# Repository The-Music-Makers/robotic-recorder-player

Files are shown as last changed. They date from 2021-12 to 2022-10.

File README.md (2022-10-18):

# Music Makers

## Robotic Recorder Player

This project is an open source hardware project that is intended to be an automated way to play a recorder instrument. Build it for yourself and use the [Python Interface](Python_Interface) to send your MIDI files to the robotic recorder player and hear them played on the recorder!

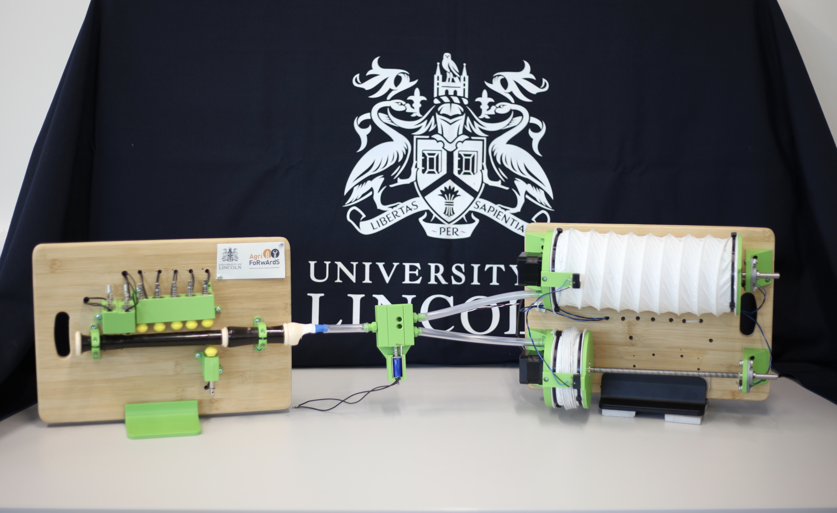
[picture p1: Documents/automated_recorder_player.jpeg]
robotic-recorder-player-image


### Demonstration

https://user-images.githubusercontent.com/53816688/196008536-8c850554-d10a-48c4-a584-36b9e6b4f8ee.mp4

### ICMC 2022 Presentation

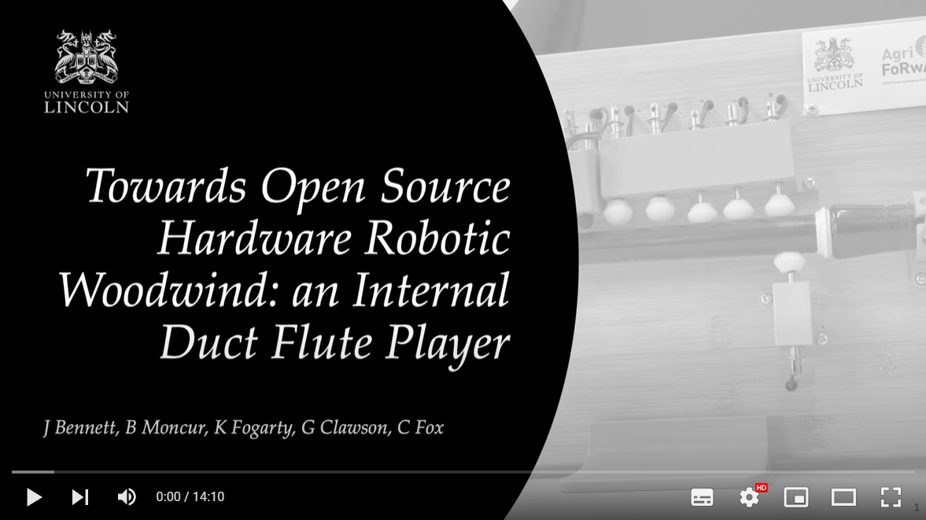
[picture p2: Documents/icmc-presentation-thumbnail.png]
ICMC presentation thumbnail click to visit YouTube presentation (https://www.youtube.com/watch?v=91aKZUQ2KXA)


## How to Build and Use

This project had been designed so that it only requires a limited toolset and you don't have to be an expert to build it. An overview is below but more detailed instructions can be found in each folder.

### Tools Required
- FDM 3D Printer and slicer software such as [Cura](https://ultimaker.com/software/ultimaker-cura).
- Basic workshop tools including spanners, screwdrivers, allen keys, drill.
- A computer with the Arduino IDE and Python installed.

### Build process
1. Get the hardware you need (you may even have some of what you need!) and follow the [Hardware build instructions](Hardware/README.md).
3. Upload the [Firmware](Firmware) to the Arduino.
4. Load the [Python Interface](Python_Interface) onto your computer.

### Play a Song
1. Create your song in MIDI format as a `.mid` file ([guide](Python_Interface/README.md#creating-mid-files)), use one of our [examples](Python_Interface/midi_examples), or find one someone else has made.
2. Connect your computer to the robotic recorder player and use the [Python Interface](Python_Interface) to hear your song played on the recorder!

## Project Development
This is an open souce hardware project and anyone is welcome to use and develop this project in line with the licences. We also encourage anyone interested to contribute to this development, especially in the areas outlined below.

### Development Areas
These are some of the areas we intend to focus future development:
- **Double-sided or twin lung** hardware and control to allow playing with reduced pauses.
- **Half-hole thumb technique** to reach highest notes.
- **Tounging mechanism** to implement the tounging technique and achieve staccato notes.
- **Increase OSH depth** adapt the project to depend more on open source components.
- **Improved usability** through an improved, maybe graphical, user interface.
- **Improved documentation** and build instructions.
- **Increased robotic intelligence** such as giving foresight of notes to make decisions on breathing.
- **Expanded scope of calibration** to include timing and facilitate robot musicians playing together.

### How to Contribute

Contributing to the project is easy and we encourage anyone who is interested to make pull requests. 

The general process of contributing on GitHub is widely documented however the outline process is below:

1. Identify where you want to host the project locally. This could be a Music Makers projects folder for example. 

1. Clone or fork the repository using GitHub desktop or the CLI into this location (CLI is recommended as this helps you become more familiar with Git in general). You can do this with the following command:

    ```bash
    git clone https://github.com/ICMC22-tmp/OSH_Automated_Recorder
    ```

1. Update the project and then make a pull request!

## Citation

If you use this project for research, please cite [the paper](https://eprints.lincoln.ac.uk/id/eprint/49154/):

```
@inproceedings{bennett2022towards,
  title={Towards Open Source Hardware Robotic Woodwind: an Internal Duct Flute Player},
  author={Bennett, James and Moncur, Bethan and Fogarty, Kyle and Clawson, Garry and Fox, Charles},
  booktitle={International Computer Music Conference, ICMC; 2022 Jul 3-7}, 
  year={2022},
  %organization={International Computer Music Association}
}
```

## Other Robotic and Autonomous Music Players

Just for fun we thought it would be interesting to include other robotic music players. They range from the sublime to the wacky, but each one is beautiful. 

- Shimon, the robotic marimba player https://www.shimonrobot.com
- Squarepusher x Z-Machines https://www.youtube.com/watch?v=VkUq4sO4LQM&t=66s
- Andrew Henry's self playing guitar https://www.youtube.com/watch?v=I_BBCmcAXcs
- Yamaha Disklavier self playing robot piano https://www.youtube.com/watch?v=m_GROsS4I7A
- Waseda Flutist Robot https://www.youtube.com/watch?v=jx8U1FgILCE
- The original Flute automaton - Floutiste https://www.youtube.com/watch?v=1TxrjpWGRXU
- A variety of robotic players including violin, piano, guitar, bongos, xylophone and others https://www.youtube.com/watch?v=rwh_acqT6J0
- Wintergaten - Marble machine https://www.youtube.com/watch?v=IvUU8joBb1Q
- Automatica - Robots Vs Music https://www.youtube.com/watch?v=bAdqazixuRY
- Music genie - Hierarchical Music https://www.youtube.com/playlist?list=PLjrJD5nSYNjoQebwV7TWPe83k7g2FjIO6

## Acknowledgements

The inspiration for this project was Andrew Henry's <a href="https://gitlab.com/Andrew_Henry/automated-guitar">automated guitar player</a>.

## Licences

This is an open-source project and licences have been chosen so to give you the freedom to use, modify, and share this project. The licences also protect the project (by ensuring contributions remain open) and its contributors (by limiting liability and warranty). Please read the licences; helpful summaries are linked below and copies of the full licences are found in the repository root. 

Software is licensed under the [GNU General Public License v3.0](https://choosealicense.com/licenses/gpl-3.0/) [`LICENCE_GNU-GPL-3.0`](LICENCE_GNU-GPL-3.0). Hardware is licensed under the [CERN Open Hardware Licence Version 2 - Weakly Reciprocal](https://choosealicense.com/licenses/cern-ohl-w-2.0/) [`LICENCE_CERN-OHL-W-2.0`](LICENCE_CERN-OHL-W-2.0). The other content of this repository including images, media, documentation, examples, sample MIDI files and anything not licensed under the other licences is licenced under the [Creative Commons Attribution Share Alike 4.0 International](https://choosealicense.com/licenses/cc-by-sa-4.0/) [`LICENCE_CC-BY-SA-4.0`](LICENCE_CC-BY-SA-4.0).

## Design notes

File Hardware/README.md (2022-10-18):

# Hardware
You can either build the system as is or you may need to modify the design to fit your recorder. Please see [Modifying the Design](#modifying-the-design) for instructions.

## You Will Need

- 1 x Recorder - we used the Aulos A205.
- 1 x [Blowing Module](Blowing%20Module).
- 1 x [Fingering Module](Fingering%20Module).

## Assembly Instructions
1. Gather and make everything required in the 'You Will Need' list according to the instructions within each module.
2. Insert the recorder into the Fingering Module.
3. Push the mouthpiece connector of the Blowing Module onto the recorder mouthpiece.
4. Connect ground, SDA and SCL between the Arduinos of the Blowing and Fingering modules.

## Modifying the Design
If you need to modify the design (for example the tone hole spacings on your recorder are different) the source of our CAD models is given using STEP files which can be found in each module's folder. These can be downloaded and edited using your favourite CAD platform. [FreeCAD](https://www.freecadweb.org/index.php) is a good open source option.

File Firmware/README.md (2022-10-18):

# Music Makers

The main script that needs to be uploaded to the Arduino board is located within the `arduino_main` folder of this directory. To upload the sketch we recommend that you use the Arduino IDE, which can be obtained from [arduino.cc](https://www.arduino.cc/en/software).

## Getting started

### `arduino_main.ino`
1. Open the Arduino IDE and load in the `arduino_main.ino` file (`File -> Open -> select_file`).
1. Ensure `solenoidPins` are set to what they were plugged in to during the hardware build.
1. Set `channel` (default `0`).
1. Ensure the notes you desire to play are defined in `notes` and `lowNote` and `highNote` are defined accordingly.
1. Upload the sketch (see [below](#upload))

### `arduino_lung.ino`
1. Open the Arduino IDE and load in the `arduino_main.ino` file (`File -> Open -> select_file`).
1. Ensure DIR, STEP and all four limit pin connections are set to what they were plugged in to during the hardware build for both stepper motor drivers.
1. Upload the sketch (see [below](#upload))

## Upload

The firmware can be uploaded through `Sketch -> Upload` or by pressing the upload button.


Connect the Arduino board to the computer and set the port it is attached to:
  
- `Tools -> Board -> Arduino AVR Boards -> *Select the Arduino Board*`
- `Tools -> Processor -> *Select the Arduino Prosessor*`
- `Tools -> Port -> *Select the USB port*`

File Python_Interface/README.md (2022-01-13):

# Python Interface

## Getting Started

### Prerequisites
Some additional libraries are required to allow the program to run these are:

- [python 3.7](https://www.python.org/downloads/release/python-370/) is required to run the Python API
- The [time](https://docs.python.org/3/library/time.html#module-time) library is used to provide the timing and delays in the python script.
- The [pyserial](https://pyserial.readthedocs.io/en/latest/pyserial.html) library is used to provide the backends support to connect to the Aurdino.
    - To install open a command terminal and type `python -m pip install pyserial`
- [MIDO](https://mido.readthedocs.io/en/latest/#) is required for working with MIDI messages and ports
    - To install open a command terminal and type `pip install mido`

### Building
To build the code download the python Python API and run through ether the command prompt or an IDE such as Spyder.

## Using the `jukebox_testing.py` utility

A small, hacky, but helpful utility to aid in testing by making it easier to send MIDI data to the Arduino and read any messages it sends back. To use:
1. Set `Raspberry_Pi/` as the current directory.
2. Ensure the Serial port is correct in `jukebox_testing.py`. Your serial port can be found by `Arduino -> Tools -> Port` or in the bottom right of your Arduino sketch console. 
3. Enter an interactive python session (by executing `python3` in your command line).
4. Run `from jukebox_testing import *`.
5. Use as described by the prompts given.

### Functions Description  
There are two primary functions provided by the utility. One to send a single MIDI message and one to play a MIDI file. Their usage is explained in the utility and below:

- Msg(msg) where msg is a mido message object e.g msg = mido.Message('note_on', note=60, velocity=64). The use the command first create your message then use sendMsg(msg) to send the newly created note to the recorder and also print anything the arduino sends to the command line.
- To play a MIDI file use the playFile(filename) command. The working directory must  be the music_makers repo root and the MIDI file must be saved in  midi_examples. Specify filename as a string and the function will print anything the arduino sends to the command line.

Help at anytime can be found by using the command showHelp().

## Creating `.mid` Files

The [examples](midi_examples) folder contains some example MIDI files. You can create your own too.

The MIDI files were created using Aria Maestosa, an open-source (GPL) MIDI sequencer/editor (https://ariamaestosa.github.io/ariamaestosa/docs/index.html). The system uses the MIDI numbering whereby MIDI note 60 corresponds to Middle C, also known as C4 which has a fundametnal frequency = 261.63 hz (https://www.inspiredacoustics.com/en/MIDI_note_numbers_and_center_frequencies). To compose a simple tune for the system, download a MIDI sequencer/editor (Aria Maestosa runs on Mac OS X, Windows and Linux/Unix), select the tempo for the composition, add the notes to the sequencer, and export the track as a MIDI file. 

## The Raspberry Pi
### Connecting to the Raspberry Pi

The Raspberry Pi 4B, nicknamed <code>jukebox</code>, has been configured such that it can run headless over WiFi. Furthermore, forwarding has been configured such that any network connected to the <code>eth0</code> port will forward to the <code>wlan</code> port (i.e: Connecting the ethernet port to the University network will allow internet access over the broadcasted WiFi).

The Raspberry Pi automatically broadcasts on the SSID: <code>jukebox</code> when it boots up, the password to connect to the wireless hotspot is <code>password</code>.

The Raspberry Pi is enabled to support SSH (Secure Shell) and VNC (Virtual Network Computing).

### SSH

To launch a secure shell connection, open a new terminal and use the command:
<br></br>
<code>ssh pi@jukebox.wlan</code> or <code>ssh pi@10.20.1.1</code>
<br></br>
The Raspberry Pi uses <code>port 22</code> (default) for SSH. You will then be prompted to enter the Raspberry Pi's local password, which is <code>password</code>. 

### VNC

To connect to the GUI, you can use the <a href="https://www.realvnc.com/en/connect/download/viewer/">REALVNC Viewer</a>. Once installed, simply enter the IP address of the Raspberry Pi (<code>10.20.1.1</code>) and then the local system username (<code>pi</code>) and password (<code>password</code>) when prompted.

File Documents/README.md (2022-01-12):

# Music Makers

## Documents
This folder contains documents that are used across the rest of the GitHub such as wiring diagrams

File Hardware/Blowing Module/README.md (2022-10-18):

# Blowing Module

<p float="left">
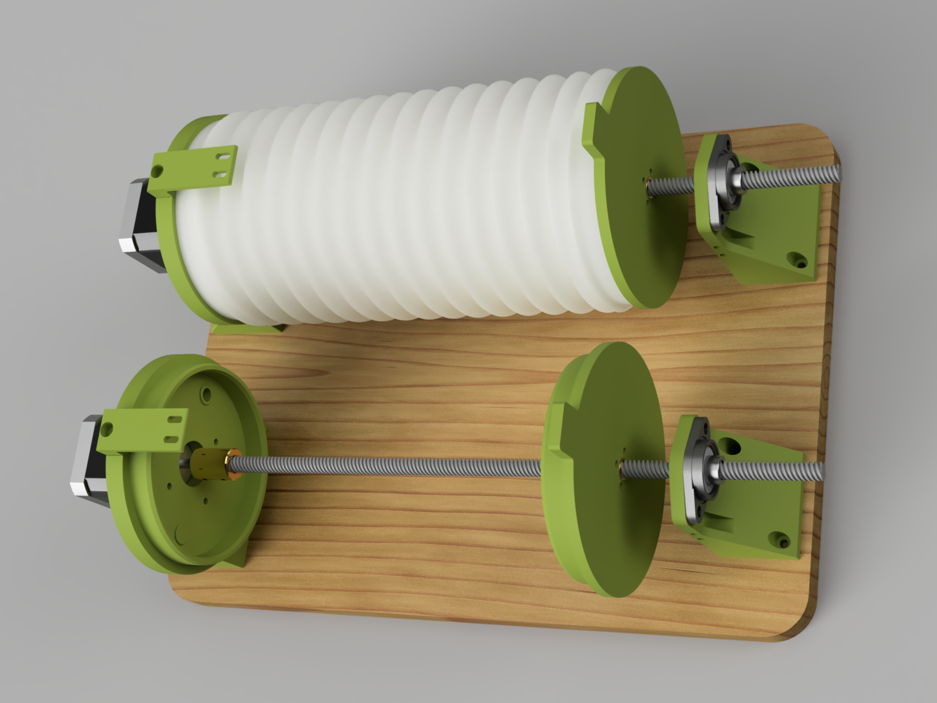
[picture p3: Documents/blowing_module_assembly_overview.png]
  
</p>
<p float="left">
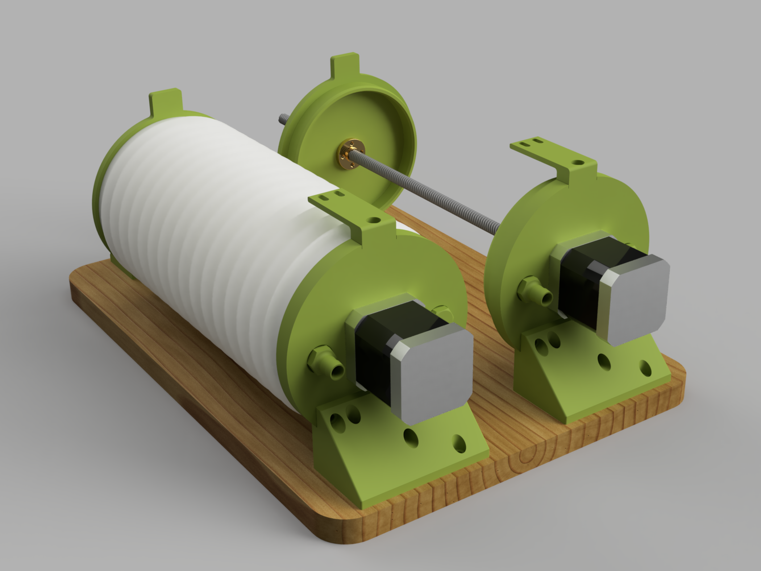
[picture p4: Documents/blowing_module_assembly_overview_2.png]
  
</p>

## Bill of Materials

### Purchase
| Item | Quantity | Details | Example Supplier |
| --- | --- | --- | --- |
| Board (plywood or breadboard) | 1 | 350 x 250 x 15 mm | |
| Stepper Motor | 2 | NEMA 17, 4 wire | [Ooznest](https://ooznest.co.uk/product/nema17-stepper-motors/?attribute_pa_model=1-8-1703hs168a-62oz-1-68a)|
| Lead screw | 2 | 8 mm lead, 290 mm | [Ooznest](https://ooznest.co.uk/product/acme-8mm-lead-screw/?attribute_pa_screw-length=290mm)|
| Lead screw nut | 2 | | [Ooznest](https://ooznest.co.uk/product/acme-nut/) |
| Lead screw to motor coupler | 2 | | [Ooznest](https://ooznest.co.uk/product/rigid-motor-shaft-coupler/?attribute_pa_size=5x8mm) |
| Bearing | 2 |  Flange[^bearing] bearing, 8 mm ID ||
| M3 x 20 mm bolt and nut | 8 | | [Kayfast](https://www.kayfast.co.uk/category/537/Metric-Socket-Cap-Screws) |
| M3 x 16 mm bolt | 8 | | [Kayfast](https://www.kayfast.co.uk/category/537/Metric-Socket-Cap-Screws) |
| M5 x 25 mm bolt and nut | 4 | | [Kayfast](https://www.kayfast.co.uk/category/537/Metric-Socket-Cap-Screws) |
| M3 x 8 mm bolt | 8 | | [Kayfast](https://www.kayfast.co.uk/category/537/Metric-Socket-Cap-Screws) |
| Pan head wood screw | 16 | 1/2" x no.6 (12 mm x 3.5 mm) | [Toolstation](https://www.toolstation.com/self-tapping-pan-head-pozi-screw/p74035) *or* [Kayfast](https://www.kayfast.co.uk/category/584/Pozi-Pan-Self-Tapping-Screws)|
| Limit switch | 4 |  | Ooznest |
| Arduino Uno | 1 | | |
| DRV8825 motor driver | 2 |  |
| 100 uF capacitor | 1 |  |
| 12V 2A power supply | 1 |  |
| Lung walls: flexible concertina material | 2 x 300 mm | e.g Ducting Hose | [Screwfix](https://www.screwfix.com/p/manrose-pvc-flexible-ducting-hose-white-1m-x-100mm/17297)|
| Cable ties | 4 | 450 mm long | |
| 8 mm tubing | 200 mm |  | |
| Stripboard, wires, connectors *OR* breadboard[^breadboard] and jumper wires |  |  |

[^breadboard]: Whilst a breadboard can be used, we recommend soldering to a stripboard for reliability.
[^bearing]: A pillowblock bearing could also be used if the bearing support was modified but we had flange bearings so used them.

### Make
| Item | Quantity | Method | Model |
| - | - | - | - |
| Bottom cap | 2 | 3D Print | [`bottom-cap.3mf`](bottom-cap.3mf) |
| Bottom cap support | 2 | 3D Print | [`bottom-cap-support.3mf`](bottom-cap-support.3mf) |
| Top cap | 2 | 3D Print | [`top-cap.3mf`](top-cap.3mf) |
| Limit switch mount | 2 | 3D Print | [`limit-switch-mount.3mf`](limit-switch-mount.3mf)
| Hose fitting | 2 | 3D Print | [`hose-fitting.3mf`](hose-fitting.3mf)
| Plug fitting | 2 | 3D Print | [`plug.3mf`](plug.3mf)|
| Mouthpiece connector | 1 | 3D Print | [`pipe-to-mouthpiece.3mf`](pipe-to-mouthpiece.3mf)|

All of our parts were printed in PLA. 0.4 mm nozzle, 0.2 mm layer height, 2 walls, 20% infill are adequate settings. No supports should be necessary if part are printed in the correct orientation.

### Combining air
A major limitation of the current implementation is no effective way to combine the air streams from the two lungs. We have experimented with off the shelf one way valves (passive solution) but they took too much pressure to overcome. We have also tried building a solenoid actuated diverter 4/2 valve (active solution) but was too leaky or took too much force to actuate. Experimentation is ongoing in the lung-hardware branch. A passive solution is preferred that is low cost and open source friendly.

## Assembly Instructions

<!-- <p float="left">
  <img src="../../Documents/blower_circuit_diagram.png" height="400" />
</p> -->

1. Obtain and make all the parts listed above.
1. Attach the bottom cap to its support with pan head screws.
1. Secure the bottom cap and support to the board with pan head screws.
1. Attach the motor to the bottom cap using M3 x 16 mm screws.
1. Join the lead screw to the motor shaft with the coupler.
1. Slide the lung wall over the lead screw.
1. Insert the lead screw nut into the top cap and secure with M3 x 20 mm screws. Thread the assembly onto the lead screw.
1. Attach the bearing to the bearing support with M5 x 25 mm screws and slide over the lead screw.
1. Line up the bearing so it is inline with the shaft and lead screw, secure the bearing support to the board with pan head screws and tighten the bearing grub screws onto the lead screw.
1. Attach the lung walls to the top and bottom cap using cable ties.
1. Attach the limit switch mount to the bottom cap with a pan head screw.
1. Attach the limit switches to the mount and bearing support using the M3 x 8 mm screws.
1. Thread the hose fitting and plug fitting into the base
1. Push the 8 mm tubing onto the fitting and the mouthpiece connector onto the tubing.
1. Repeat steps 2 to 14 for the other lung.
1. On a using stripboard or a breadboard, connect each stepper motor to a motor driver, and the power supply and capacitor as detailed on the [DRV8825 page](https://www.pololu.com/product/2133).
1. Connect 5V, GND, STEP, DIR pins of the driver to the Arduino, noting the pin numbers.
1. Wire the limit switches in N.O. configuration with one lead to ground and the other to a pin on the Arduino, noting the pin number.
1. Prepare a cable to connect the GND, and I2C (SCL & SDA) lines of the Arduino to the Arduino of the Fingering Module.

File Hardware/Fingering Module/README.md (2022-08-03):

# Fingering Module

<p float="left">
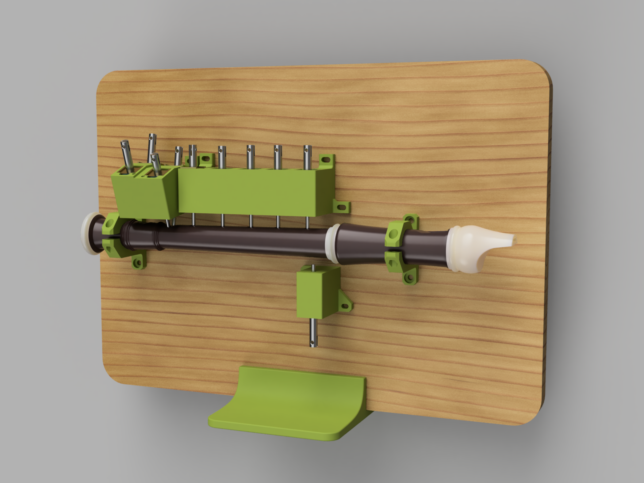
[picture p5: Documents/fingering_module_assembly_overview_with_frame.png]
  
</p>

## Bill of Materials

The robot recorder player relies on readily available hobby electronics components in the spirit of the CERN-OHL-W. The components can be changed for other makes or types but changing the components will have an effect on how each module operates, for some types of woodwind instruments changes may be needed to allow the modules to operate as desired. Links have been provided for UK suppliers for the components used to create the module, these suppliers are not the only source of the components and they can be bought from other suppliers or locations.

### Purchase
| Item | Quantity | Details | Example |
| - | - | - | - |
| Arduino Mega | 1 | | [UK](https://www.amazon.co.uk/ELEGOO-Controller-ATmega2560-ATMEGA16U2-Compatible/dp/B06XKMZ3T9/)|
| Power Supply | 1 | ~~12V, 10A~~ [^voltage] | [UK](https://www.amazon.co.uk/SHNITPWR-100V-240V-Converter-Transformer-5-5x2-5mm/dp/B08BJRN5SX/)|
| Solenoid | 10 | Model: JF-0530B, 12V | [UK](https://www.amazon.co.uk/Rtengtunn-JF-0530B-Push-Pull-Gangbei-0530B-Electromagnet/dp/B08291L2XL/)|
| TIP120 Darlington Transistor | 10 | | [UK](https://www.amazon.co.uk/BOJACK-Epitaxial-Transistor-Darlington-Transistors/dp/B08D8SJPCG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)|
| 1K Ohm Resistor | 10 | | [UK](https://www.amazon.co.uk/sourcing-map-Metal-Resistors-Tolerances/dp/B07LGM23Y4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)|
| 1N4001 Diode | 10 | | [UK](https://www.amazon.co.uk/ExcLent-100Pcs-1N4001-50V-Diode/dp/B07J3ZT55G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)|
| Stripboard[^breadboard], wires, connectors | | Stipboard or perfboard depending on preference | |
| Pan head wood screw | 22 | 12 mm x 3.5 mm | [UK](https://www.toolstation.com/self-tapping-pan-head-pozi-screw/p74035) |
| M3 x 25 mm bolt and nut | 4 | | [UK](https://www.amazon.co.uk/Screw-Bolts-Stainless-Steel-340pcs/dp/B08RRW6B3H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)|
| Board (plywood or breadboard) | 1 | 350 x 250 x 15 mm | |

[^voltage]: If the solenoids are run continuously at 12V they will overheat. Currently the system is being run at 8V but we intend to implement a PWM solution so 12V can be used for initial actuation then 8V for a holding current.

[^breadboard]: Note, a breadboard cannot be used here as it won't handle the current.

### Make
| Item | Quantity | Method | Model |
| - | - | - | - |
| Holder Foot End | 1 | 3D Print | [`holder_foot.3mf`](holder_foot.3mf) |
| Holder Head End | 1 | 3D Print | [`holder_head.3mf`](holder_head.3mf) |
| Five Finger Box | 1 | 3D Print | [`finger-box_five.3mf`](finger-box_five.3mf) |
| Thumb Finger Box | 1 | 3D Print | [`finger-box_thumb.3mf`](finger-box_thumb.3mf) |
| Double Tone Hole Finger Box | 1 | 3D Print | [`finger-box_double-hole.3mf`](finger-box_double-hole.3mf) |
| Stand | 1 | 3D Print | [`stand.3mf`](stand.3mf) |

All of these parts were printed in PLA. 0.4 mm nozzle, 0.2 mm layer height, 2 walls, 20% infill are adequate settings. Supports aren't required if they are printed in the correct orientation. The files are supplied in 3MF format (see issue https://github.com/The-Music-Makers/music_makers/issues/45) which mainstream slicers will load.

### Fingertips
It is necessary to put a soft material on the end of the solenoid plungers to protect the recorder and ensure an adequate seal. They are still in the experimental stage and details of our attempts and ideas are below.

1. **Foam ear plugs.** A hole can be made in the end and they can be glued to the plunger.
2. **3D Printed Flexible Filament.** Print the following parts in a flexible filament.
    | Item | Quantity | Model |
    | - | - | - |
    | Main fingertip | 6 | [`finger-tip_main.3mf`](finger-tip_main.3mf)|
    | Double tone hole large fingertip | 2 | [`finger-tip_double-big.3mf`](finger-tip_double-big.3mf)|
    | Double tone hole small fingertip | 2 | [`finger-tip_double-small.3mf`](finger-tip_double-small.3mf)|

    We used TPU with a shore hardness of 95A. They were printed in vase mode but with 3 mm of bottom layers. This results in a solid bottom which will screw onto the plunger and a hollow top which will deform to the tone holes.
3. **Casting silicone.** We would like to try casting silicone fingertips.

## Assembly Instructions
1. Obtain and make all the parts listed above.
1. Attach the head and foot holder to the board with pan head screws, insert the recorder and use the M3 bolts and nuts to secure.
1. Insert the solenoids into the finger boxes and secure with a pan head screw if loose.
1. Attach fingertips to the solenoid plungers.
1. Line up the finger boxes to the recorder and attach to the board with pan head screws.
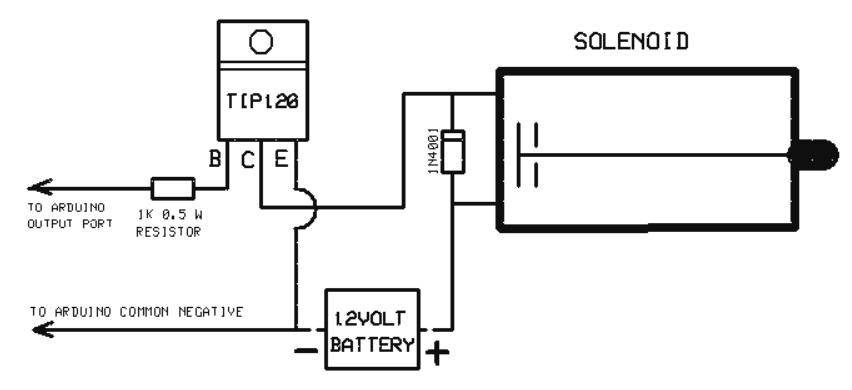
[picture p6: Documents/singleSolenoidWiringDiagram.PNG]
1. The solenoids need to be connected to the power supply and Arduino (plus the resistor, diode and transistor) as per the following diagram.  We drilled holes in the board to pass the solenoid wires through and connected everything on stripboard. Each solenoid circuit as per the image needs to be connected to a different output pin of the Arduino, noting the pin number.

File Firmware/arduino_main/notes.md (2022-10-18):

# Notes for Arduino sketch

- Note velocity not currently handled. The plan is to map blowing velocity of MIDI message to a motor acceleration (in steps/s^2 ?). The motor speed will ramp up and down to the set RPM.
- For initial testing purposes, only notes C5 to D6 implemented. Any notes sent outside this range will be ignored.
- Testing showed we wanted to keep fingers energised after a note on but if that was infinite then overheating occured. Currently a 2 second delay is hard coded which is undesirable. If heating issues fixed then could keep energised and decode an end of song MIDI message.
- Target frequency currently not utilised but plans exist to do so.

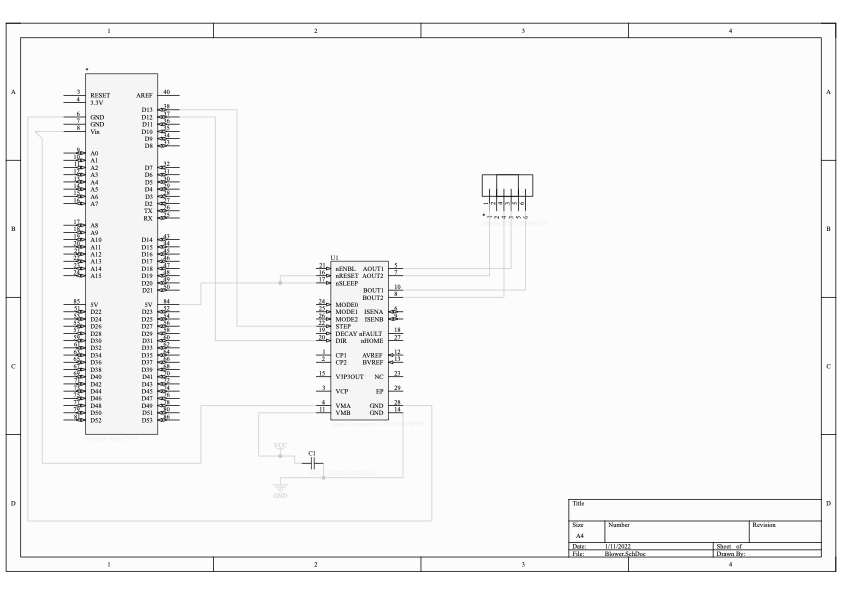
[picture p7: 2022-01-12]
Documents/blower_circuit_diagram.png

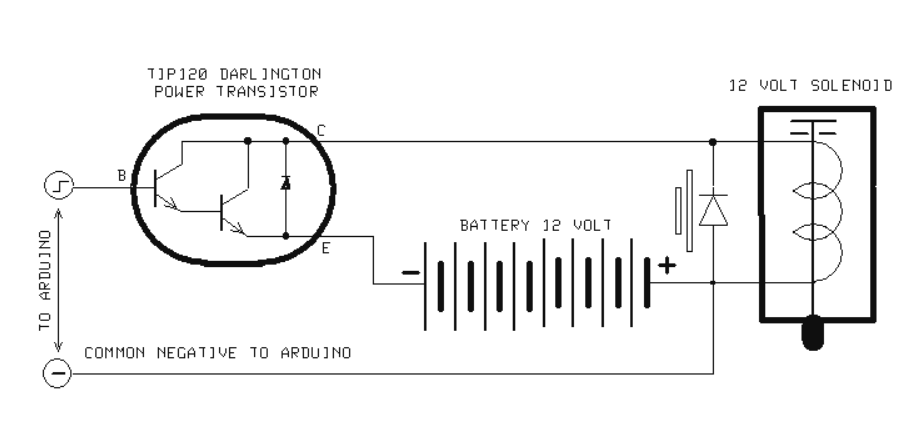
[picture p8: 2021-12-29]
Documents/singleSolenoidCircuitDiagram.PNG

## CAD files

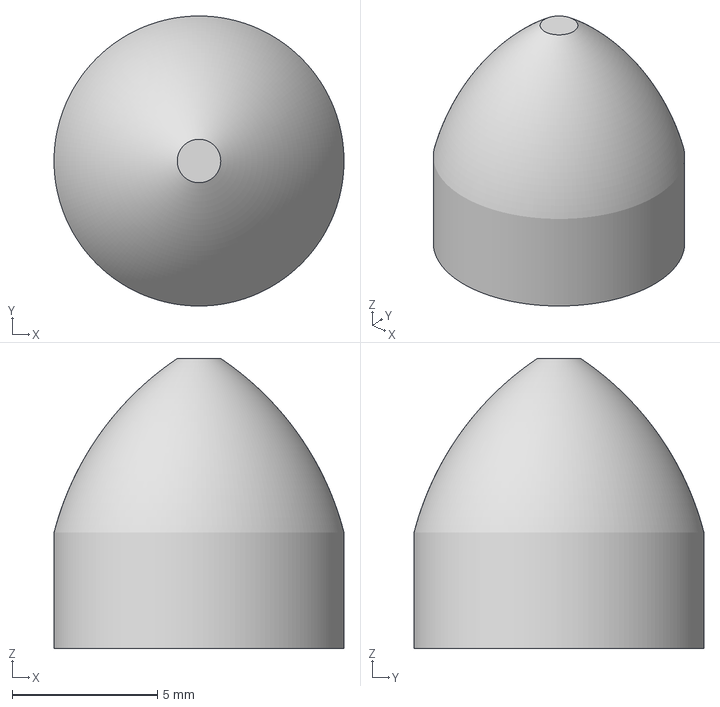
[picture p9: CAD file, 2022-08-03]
Hardware/Fingering Module/finger-tip_main.3mf
10.00 x 10.00 x 10.0 mm

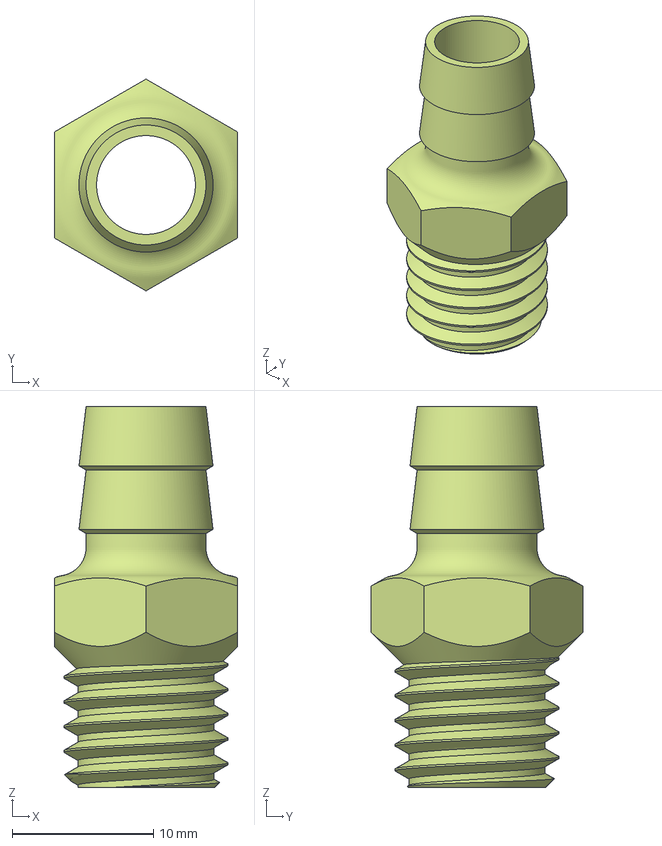
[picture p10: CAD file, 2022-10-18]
Hardware/Blowing Module/hose-fitting.3mf
13.0 x 15.0 x 27.0 mm

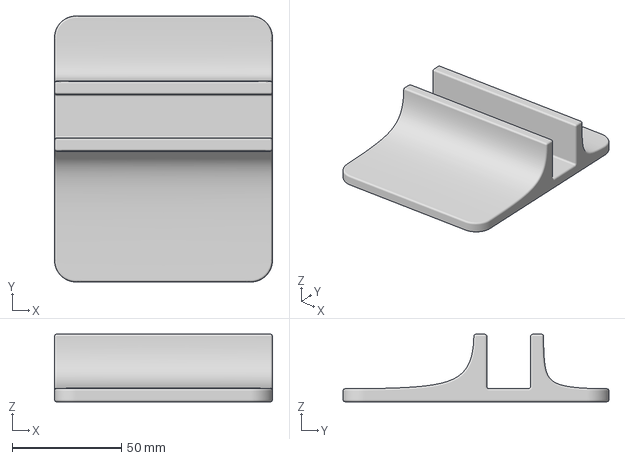
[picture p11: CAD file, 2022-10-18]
Hardware/Fingering Module/Stand v1.3mf
100.0 x 122.0 x 31.0 mm

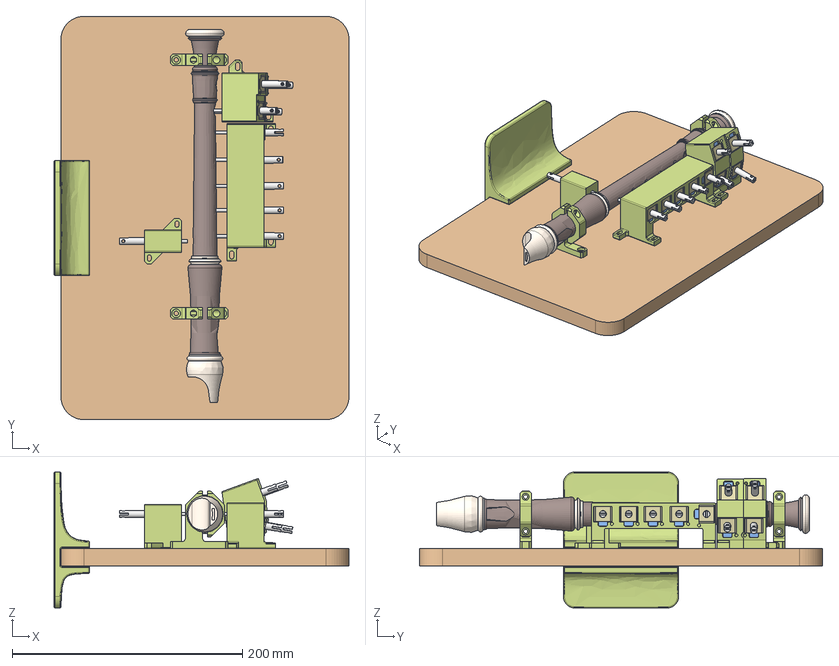
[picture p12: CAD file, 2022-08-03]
Hardware/Fingering Module/STEP Files/Fingering Module.step
256.0 x 350.0 x 118.0 mm
base_frame
Mouthpiece
Middle bit
End
recorder_clamp_bottom v10 (1)
recorder_clamp_bottom v10 (1) (1)
plunger x 10
thumb box
Stand

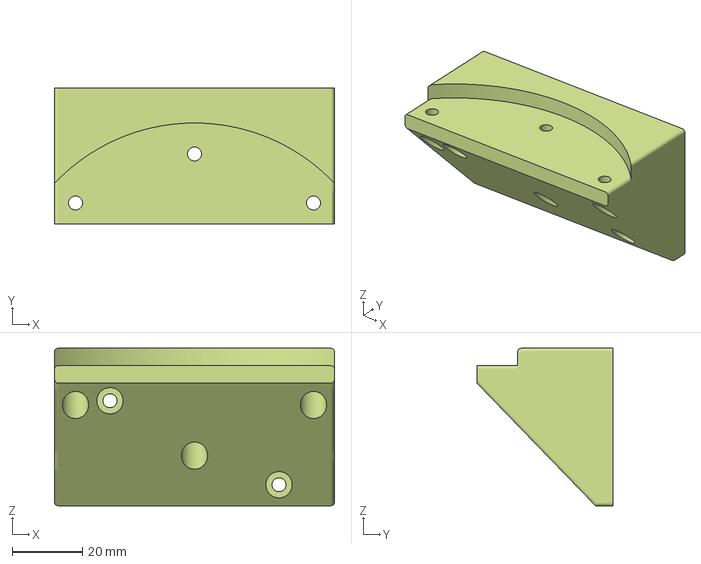
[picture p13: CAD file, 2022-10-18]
Hardware/Blowing Module/bottom-cap-support.3mf
80.0 x 38.9 x 45.0 mm

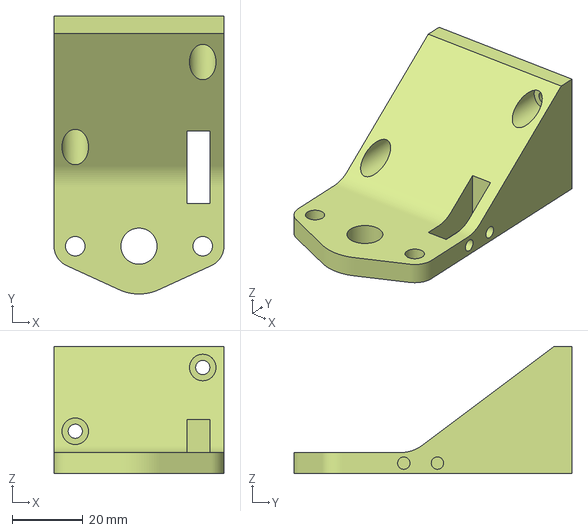
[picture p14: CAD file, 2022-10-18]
Hardware/Blowing Module/bearing-support.3mf
48.0 x 78.5 x 36.0 mm

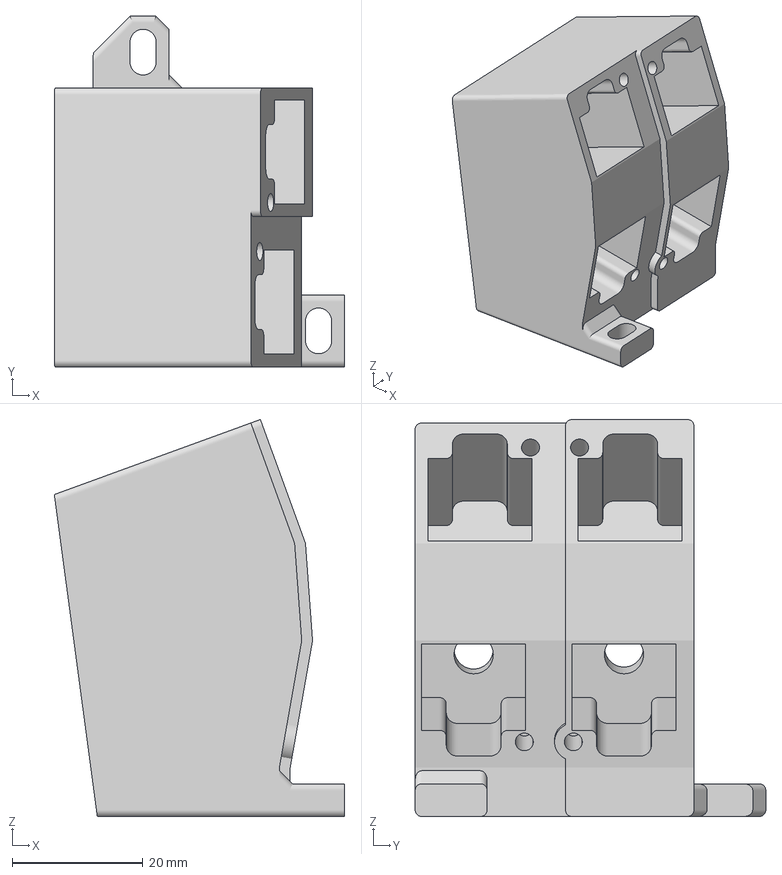
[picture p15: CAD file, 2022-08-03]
Hardware/Fingering Module/finger-box_double-tone.3mf
44.4 x 53.7 x 60.7 mm

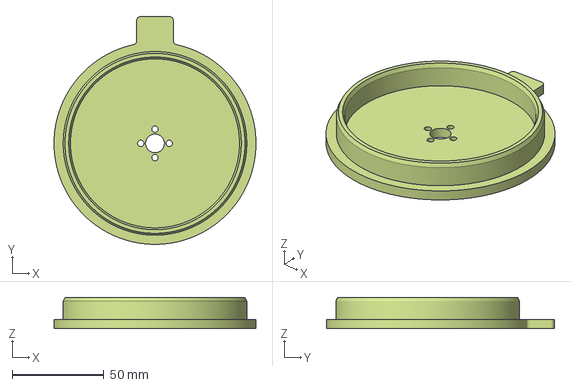
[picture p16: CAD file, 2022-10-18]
Hardware/Blowing Module/top-cap.3mf
110.0 x 124.0 x 17.0 mm

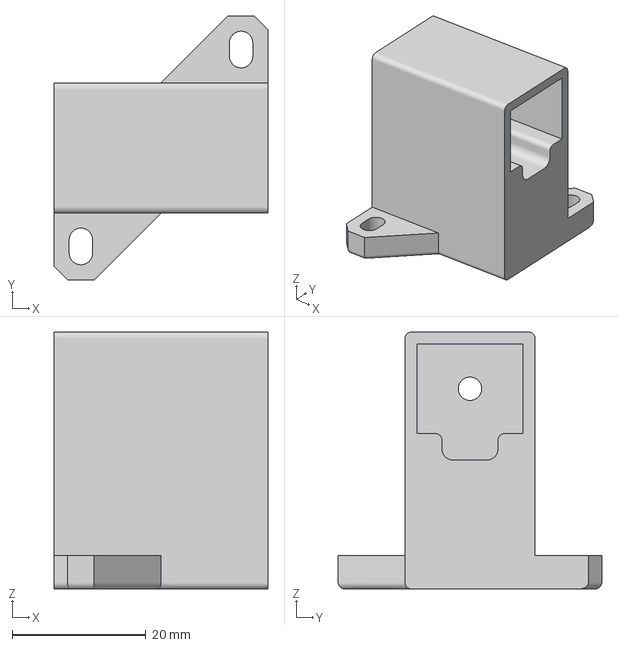
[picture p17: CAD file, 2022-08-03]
Hardware/Fingering Module/finger-box_thumb.3mf
32.0 x 39.5 x 38.5 mm

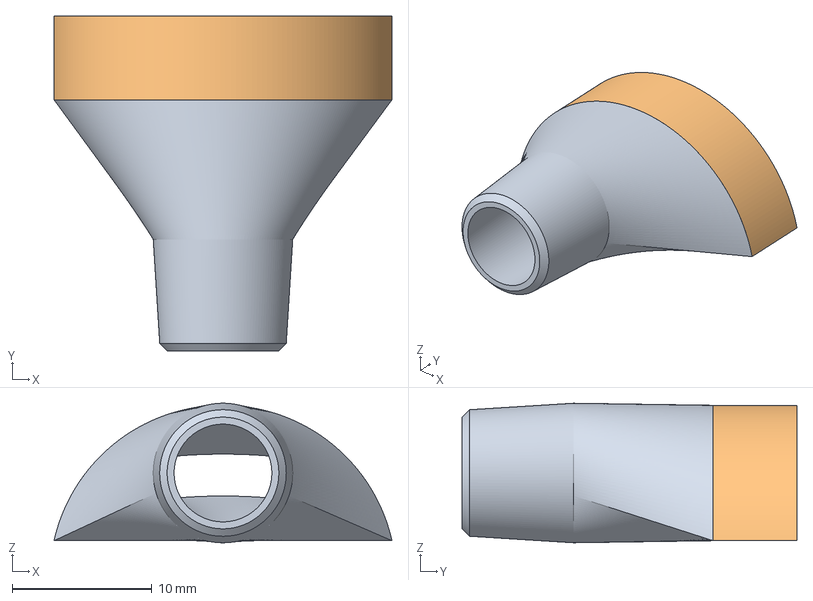
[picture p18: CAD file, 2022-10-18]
Hardware/Blowing Module/pipe-to-mouthpiece.3mf
24.2 x 24.0 x 10.0 mm
this one

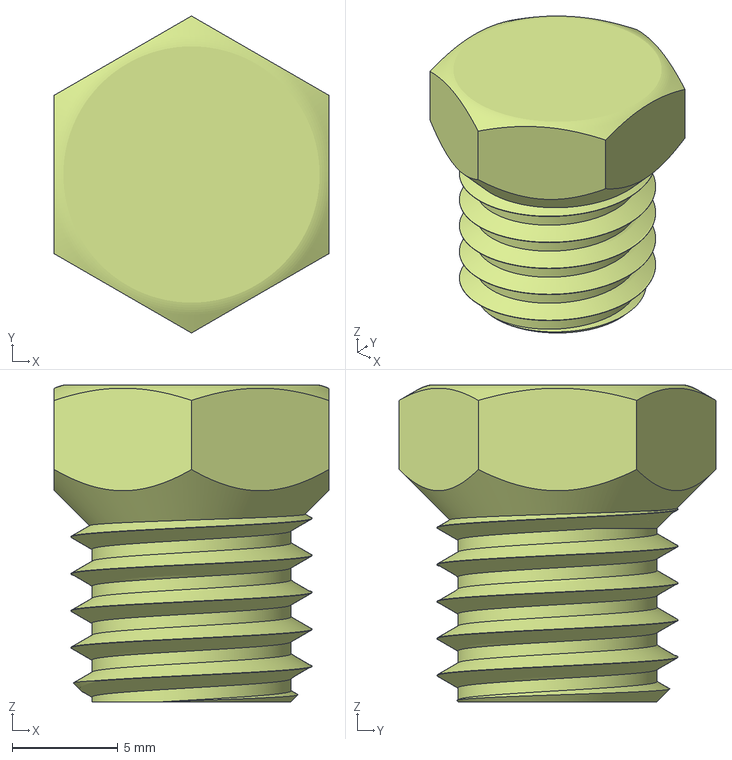
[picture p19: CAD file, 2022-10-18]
Hardware/Blowing Module/plug.3mf
13.0 x 15.0 x 15.0 mm

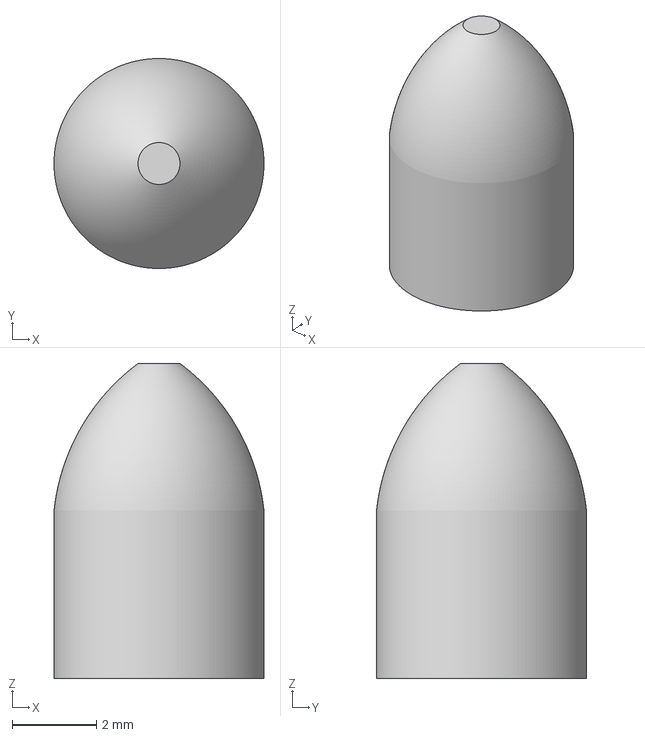
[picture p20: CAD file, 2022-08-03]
Hardware/Fingering Module/finger-tip_double_small.3mf
5.00 x 5.00 x 7.50 mm

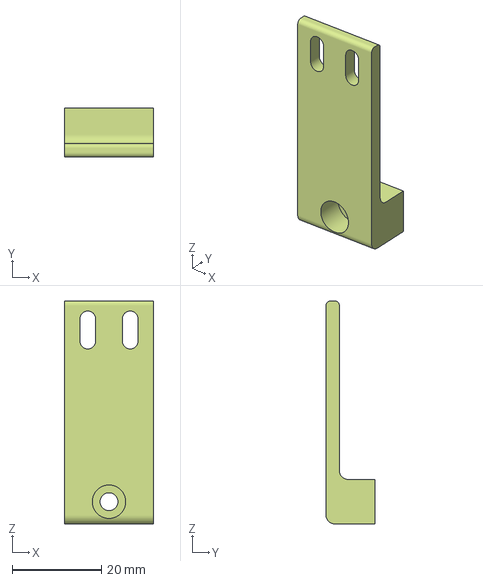
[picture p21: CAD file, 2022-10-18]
Hardware/Blowing Module/limit-switch-mount.3mf
20.0 x 11.0 x 50.0 mm

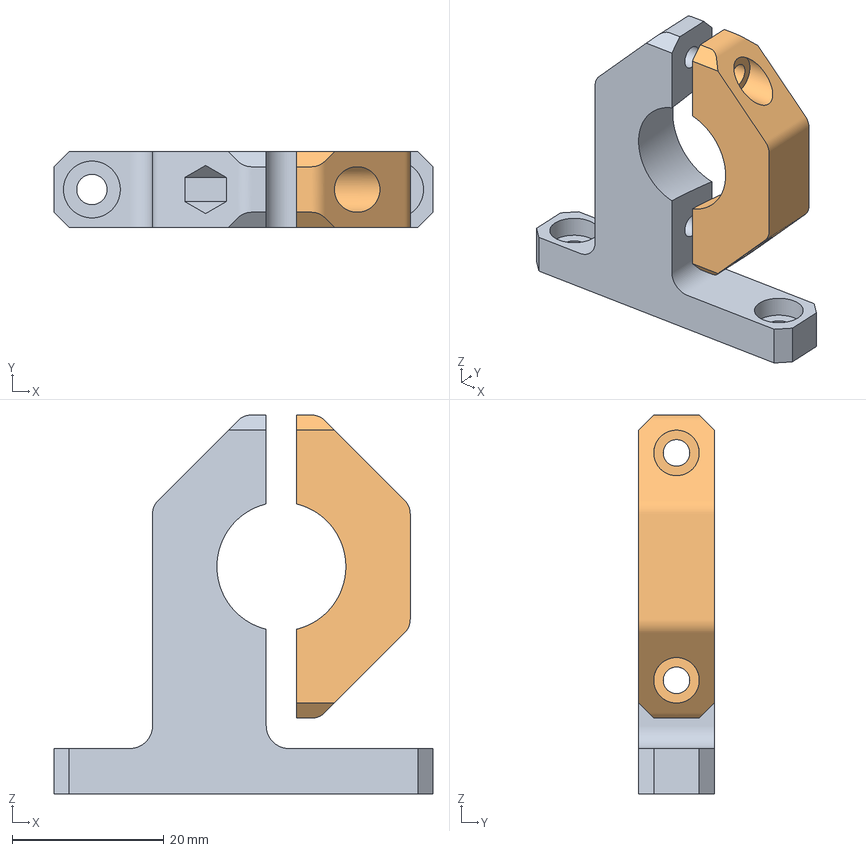
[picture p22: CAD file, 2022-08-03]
Hardware/Fingering Module/holder_foot.3mf
50.0 x 10.0 x 50.0 mm

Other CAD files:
Hardware/Blowing Module/bottom-cap.3mf
Hardware/Fingering Module/finger-box_five.3mf
Hardware/Fingering Module/holder_head.3mf
Hardware/Fingering Module/finger-tip_double_big.3mf
Hardware/Fingering Module/stand.3mf

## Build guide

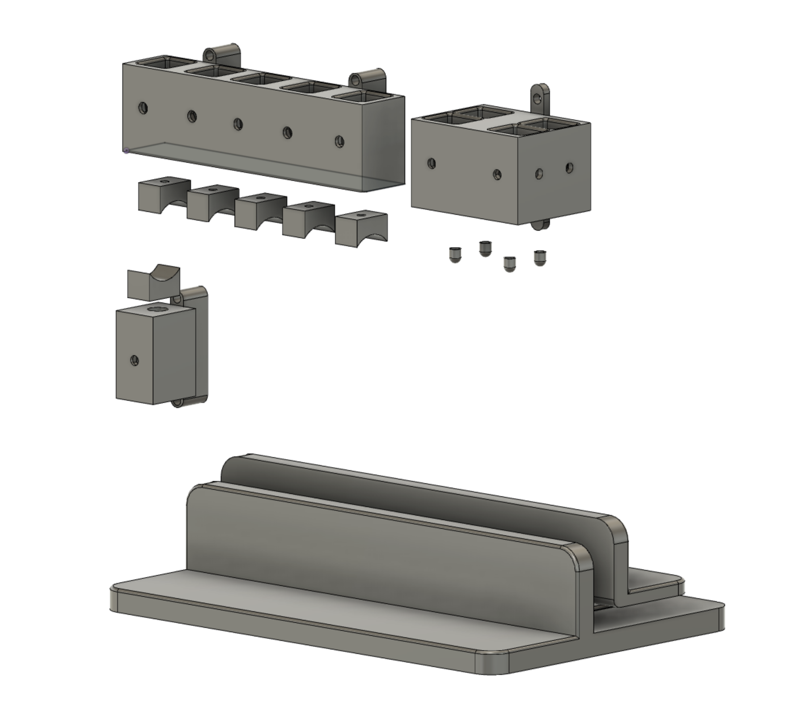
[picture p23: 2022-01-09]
Documents/fingering_module_assembly_overview.png

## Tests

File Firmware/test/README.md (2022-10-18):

# Test sketches

## ```number_sender.ino```
Use to test the ```arduino_lung.ino``` sketch. Upload to another Arduino and connect I2C between Arduinos.

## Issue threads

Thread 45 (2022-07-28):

Transition to 3MF format from STL for printed parts

bennett-j, 2022-07-28:
Many believe STL should be obsolete given the manifold advantages of 3MF. The files are much more space efficient, solve compatibility issues and include proper measurement units. Further, the 3MF standard is open source (whereas STL is not).

In the first instance upload files as 3MF, in future can explore the functionality of including print configuration settings and license data and more.

bennett-j, 2022-08-03:
The fingering module has been transitioned to 3MF files but without the more advanced functionality.

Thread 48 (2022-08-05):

Air flow from twin lung system must be combined

bennett-j, 2022-08-05:
A passive solution using off-the-shelf one-way valves has been tried but these require too much pressure to overcome. A diverter 4/2 valve system has been created and tried in `lung-hardware` branch (active solution) but is too leaky or requires too much force to actuate. Refinements to these solutions or a new solution are sought. A low cost, open source friendly solution is preferred.

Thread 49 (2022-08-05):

Home both lungs simultaneously

bennett-j, 2022-08-05:
Should be an easy fix. Needs updating in `Firmware/arduino_lung/arduino_lung.ino`.

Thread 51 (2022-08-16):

Silent stepper motor driver

Kyle-Fogarty, 2022-08-16:
In the current implementation of the system, the sound produced by the stepper motors of the lung system is audible and sometimes distracting from the sound actually being produced by the recorder. One possible method we have identified to prevent this is to implement silent stepper motor drivers, which we would be interested in somebody testing out.

bennett-j, 2022-08-16:
Have tested the TMC2208 drivers which are a near drop in replacement. The code shouldn't need changing but the perfboard will need modifying slightly, in particular, 5V to VIO pin.

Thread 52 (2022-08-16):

Balancing heat and speed

Kyle-Fogarty, 2022-08-16:
In experimenting with the current system we found that the solenoids can become very warm when operating. The amount of heat produced can of course be reduced by limiting the potential difference over the solenoid, but this has consequences on the speed and response of actuation. Ideally, we would like to engineer a solution that gives the best possible response, without getting too hot. One suggested solution is to make use of pulse width modulation (PWM) to reduce the amount of time current is supplied to the solenoid, and hence reduce the power and hopefully heat.

bennett-j, 2022-08-16:
To add to this, a possible solution may be using 12V initially to actuate the solenoid with good speed of response, then reducing to a holding voltage that keeps the finger pressed without overheating. PWM may be a good way to achieve this.

bennett-j, 2022-08-16:
Note, the system is currently run at about 8V which gives a reasonably fast response without overheating.

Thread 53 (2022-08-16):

Half-hole finger actuation

Kyle-Fogarty, 2022-08-16:
Another part of the system which we didn't fully manage to implement is half-hole actuation, which is required to achieve certain notes on the recorder.

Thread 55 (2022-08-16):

Frequency detection and calibration

Kyle-Fogarty, 2022-08-16:
One aspect of the project that we never truly got working was the automatic pitch calibration algorithm, for calibrating the RPM of the stepper motor to achieve the correct air flow rate. To achieve this, a method of measuring the frequency spectrum (or fundamental frequency of the spectrum at a minimum) produced by the recorder is required. Our aim was to do all signal processing onboard the micro-controller, but with its limited memory and speed, this is challenging. We welcome further work on this issue.

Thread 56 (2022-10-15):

Improve finger de-energising timing

bennett-j, 2022-10-15:
Currently fingers de-energise after a hard-coded 2-second delay so they are held between repeated notes but not forever. This is a temporary measure that clearly fails if notes are to be held for longer than 2 seconds. Once overheating is dealt with (#52), remove functionality in ```arduino_main.ino``` that de-energises the fingers and instead decode the end of song MIDI message and release the fingers then.

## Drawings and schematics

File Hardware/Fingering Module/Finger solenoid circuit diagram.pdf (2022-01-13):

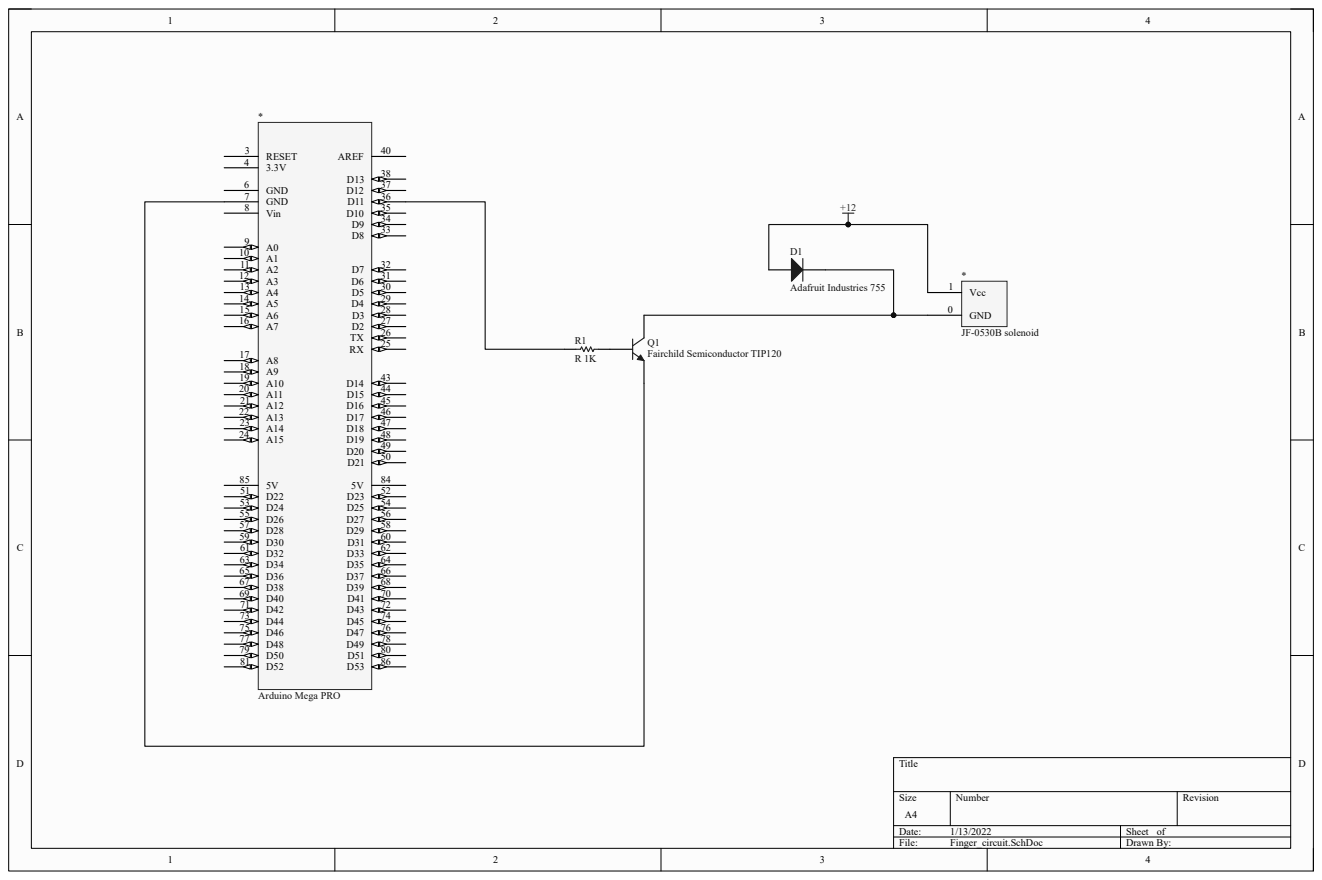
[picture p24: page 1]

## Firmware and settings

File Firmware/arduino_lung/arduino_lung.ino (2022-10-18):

/*
 *  Music Makers: Robotic Recorder Player
 *  Lung Arduino sketch
 *
 *  Copyright © 2022 Music Makers
 *
 *  This file is part of the Music Makers' Robotic Recorder Player project.
 *  The Robotic Recorder Player is an open source hardware and software
 *  project. A copy of the licences that cover this project are found in the
 *  root of this repository.
 *
 *  Description
 *  • Receives desired blowing velocity as integers via I2C.
 *  • Actuates stepper motors via drivers to turn at desired RPM
 *  • Implements a twin lung system such that one can fill while other empties.
 */

/*
 * Resources
 * https://github.com/laurb9/StepperDriver/blob/master/examples/MultiAxis/MultiAxis.ino
 * https://docs.arduino.cc/learn/communication/wire#controller-writer
 */

/*
 * Improvements:
 * 1. Use array or something for multiple motors to avoid repeated functions
 *    → or have reference variable that points to the active lung
 * 2. Use interrupts for limit pins (Uno only has 2)
 * 3. Implement switching active if within threshold of end
 * 4. ENABLE/DISABLE steppers
 */

// comment out to not compile debugging sections of code
#define DEBUG

#include "Wire.h"
#include "BasicStepperDriver.h"
#include "MultiDriver.h"


/////////////////////////
//    DECLARATIONS &   //
//      CONSTANTS      //
/////////////////////////

// for both steppers
const int MOTOR_STEPS = 200;
const int MICROSTEPS = 1;
const int HOME_RPM = 300;

// stepper A
const int DIR_A = 6;
const int STEP_A = 7;

// stepper B
const int DIR_B = 8;
const int STEP_B = 9;

// create stepper objects
BasicStepperDriver stepperA(MOTOR_STEPS, DIR_A, STEP_A);
BasicStepperDriver stepperB(MOTOR_STEPS, DIR_B, STEP_B);
MultiDriver controller(stepperA, stepperB);

// limit pins
const int LIMIT_A_EMPTY = 2;
const int LIMIT_B_EMPTY = 3;
const int LIMIT_A_FULL = 4;
const int LIMIT_B_FULL = 5;

// a number definitely more than the number of steps from full to empty
const int DEFINITELY_ENOUGH_STEPS = 10000;
// temporary fix to add to max steps and make sure it reaches switch
const int SOME_EXTRA = 400;

// number of steps from full to empty
int maxStepsA;
int maxStepsB;
// number of steps left to empty - only updated on stop()
int stepsRemA;
int stepsRemB;

bool aIsFilling = false;
bool bIsFilling = false;

char activeStepper = 'A';
bool stopped = true;

int reading = 0;


/////////////////////////
//    FUNCTION DEFS    //
/////////////////////////

void homeStepperA()
{

    // move towards home
    stepperA.startMove(-DEFINITELY_ENOUGH_STEPS);

    // while stepper not at limit pin, move towards it.
    while (digitalRead(LIMIT_A_FULL) != LOW)
    {
        stepperA.nextAction();
    }
    stepperA.stop();

#ifdef DEBUG
    Serial.println("Stepper A reached home");
#endif
}

void getMaxStepsA()
{

    // move to home position
    homeStepperA();

    // now at home set count to zero
    int steps = 0;

    // move to empty end, counting steps
    stepperA.startMove(DEFINITELY_ENOUGH_STEPS);
    while (digitalRead(LIMIT_A_EMPTY) != LOW)
    {
        stepperA.nextAction();
        steps++;
    }

    stepperA.stop();

    // set max steps
    maxStepsA = steps;

#ifdef DEBUG
    Serial.println("Stepper A ready");
#endif
}

void homeStepperB()
{
    // move towards home
    stepperB.startMove(-DEFINITELY_ENOUGH_STEPS);

    // while stepper not at limit pin, move towards it.
    while (digitalRead(LIMIT_B_FULL) != LOW)
    {
        stepperB.nextAction();
    }
    stepperB.stop();

#ifdef DEBUG
    Serial.println("Stepper B reached home");
#endif
}

void getMaxStepsB()
{

    // move to home position
    homeStepperB();

    // now at home set count to zero
    int steps = 0;

    // move to empty end, counting steps
    stepperB.startMove(DEFINITELY_ENOUGH_STEPS);
    while (digitalRead(LIMIT_B_EMPTY) != LOW)
    {
        stepperB.nextAction();
        steps++;
    }

    stepperB.stop();

    // set max steps
    maxStepsB = steps;

#ifdef DEBUG
    Serial.println("Stepper A ready");
#endif
}

// function that executes whenever data is received from master
// this function is registered as an event, see setup()
void receiveEvent(int howMany)
{
    if (2 <= Wire.available()) // if two bytes were received
    { 
        reading = Wire.read();  // receive high byte
        reading = reading << 8; // shift high byte to be high 8 bits
        reading |= Wire.read(); // receive low byte as lower 8 bits

        #ifdef DEBUG
        Serial.print("RPM Request: ");
        Serial.println(reading); // print the reading
        #endif

        // start or update blowing rpm
        if (reading > 0)
        {
            switch (activeStepper)
            {
            case 'A':
                stepperA.setRPM(reading);
                break;

            case 'B':
                stepperB.setRPM(reading);
                break;

            default:
                break;
            }

            // if we had stopped then need to start again 
            // but if not updating RPM (done above) is enough
            if (stopped)
            {
                switch (activeStepper)
                {
                case 'A':
                    stepperA.startMove(stepsRemA);
                    break;

                case 'B':
                    stepperB.startMove(stepsRemB);
                    break;

                default:
                    break;
                }
                stopped = false;
            }
        }
        // else reading == 0 and we want to stop blowing
        else
        {
            // stop the stepper currently blowing
            switch (activeStepper)
            {
            case 'A':
                stepsRemA = stepperA.stop();
                break;

            case 'B':
                stepsRemB = stepperB.stop();
                break;

            default:
                break;
            }
            stopped = true;
        }
    }
}

// // https://stackoverflow.com/a/8914714
// BasicStepperDriver& getActiveStepper() {
//     switch (activeStepper)
//     {
//     case 'A':
//         return stepperA;
//         break;

//     case 'B':
//         return stepperB;
//         break;

//     default:
//         break;
//     }
// }


/////////////////////////
//        SETUP        //
/////////////////////////

void setup()
{
    #ifdef DEBUG
    Serial.begin(115200);
    #endif

    // setup steppers
    stepperA.begin(HOME_RPM, MICROSTEPS);
    stepperB.begin(HOME_RPM, MICROSTEPS);

    // set limit pins to read HIGH unless grounded by switch closed
    pinMode(LIMIT_A_EMPTY, INPUT_PULLUP);
    pinMode(LIMIT_B_EMPTY, INPUT_PULLUP);
    pinMode(LIMIT_A_FULL, INPUT_PULLUP);
    pinMode(LIMIT_B_FULL, INPUT_PULLUP);

    // home steppers and get limits
    getMaxStepsA();
    homeStepperA();
    getMaxStepsB();
    homeStepperB();

    #ifdef DEBUG
    Serial.print("Max Steps A: ");
    Serial.println(maxStepsA);
    Serial.print("Max Steps B: ");
    Serial.println(maxStepsB);
    #endif

    activeStepper = 'A';
    stepsRemA = maxStepsA + SOME_EXTRA;
    stepsRemB = maxStepsB + SOME_EXTRA;

    // join i2c bus with address #4
    Wire.begin(4);
    // register event              
    Wire.onReceive(receiveEvent);
}


/////////////////////////
//      MAIN LOOP      //
/////////////////////////

void loop()
{
    // check limit pins
    if (digitalRead(LIMIT_A_EMPTY) == LOW && activeStepper == 'A')
    {
        // if A reaches empty whilst active
        // stop it and get RPM to transfer to B and start
        stepsRemA = 0;
        int currentRPM = stepperA.getCurrentRPM();
        stepperA.setRPM(HOME_RPM);
        aIsFilling = true;

        if (bIsFilling)
        {
            // in case it hasn't filled by now
            int remaining = stepperB.stop();
            // set the steps B will have til empty
            stepsRemB = DEFINITELY_ENOUGH_STEPS - remaining;
            bIsFilling = false;
        }
        activeStepper = 'B';
        stepperB.setRPM(currentRPM);

        #ifdef DEBUG
        Serial.println("A Empty. Starting B.");
        #endif
        
        // start A moving to home B blowing
        controller.startMove(-DEFINITELY_ENOUGH_STEPS, stepsRemB);
    }
    if (digitalRead(LIMIT_B_EMPTY) == LOW && activeStepper == 'B')
    {
        // as per above but for B empty
        stepsRemB = 0;
        int currentRPM = stepperB.getCurrentRPM();
        stepperB.setRPM(HOME_RPM);
        bIsFilling = true;

        if (aIsFilling)
        {
            int remaining = stepperA.stop();
            stepsRemA = DEFINITELY_ENOUGH_STEPS - remaining;
            aIsFilling = false;
        }
        activeStepper = 'A';
        stepperA.setRPM(currentRPM);

        #ifdef DEBUG
        Serial.println("B Empty. Starting A.");
        #endif
        
        // start A blowing and Bmoving to home
        controller.startMove(stepsRemA, -DEFINITELY_ENOUGH_STEPS);
    }
    if (digitalRead(LIMIT_A_FULL) == LOW && aIsFilling)
    {
        #ifdef DEBUG
        Serial.println("A Full");
        #endif
        
        // A is full, stop it
        stepperA.stop();
        aIsFilling = false;
        stepsRemA = maxStepsA;
    }
    if (digitalRead(LIMIT_B_FULL) == LOW && bIsFilling)
    {
        #ifdef DEBUG
        Serial.println("A Full");
        #endif
        
        // B is full, stop it
        stepperB.stop();
        bIsFilling = false;
        stepsRemB = maxStepsB;
    }

    // do the next step
    controller.nextAction();
}

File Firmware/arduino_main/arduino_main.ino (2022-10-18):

/*
 *  Music Makers: Robotic Recorder Player
 *  Main Arduino sketch
 *
 *  Copyright © 2022 Music Makers
 *
 *  This file is part of the Music Makers' Robotic Recorder Player project.
 *  The Robotic Recorder Player is an open source hardware and software
 *  project. A copy of the licences that cover this project are found in the
 *  root of this repository.
 *
 *  Description
 *  • Receives MIDI messages from a companion computer over the serial port.
 *  • Actuates solenoids to cover tone holes on the recorder, replicating the
 *    action of fingers.
 *  • Sends a blowing RPM via I2C to the lung module to produce air.
 */

// comment out to not compile debugging sections of code
#define DEBUG

#include <Wire.h>

/////////////////////////
//    DECLARATIONS &   //
//      CONSTANTS      //
/////////////////////////

// define range of notes recorder can play
const int lowNote = 72;  // C5
const int highNote = 86; // D6
const int arrSize = highNote - lowNote + 1;
// define offset such that MIDInote - offset = index for note array
// assigning to new name for readability
const int noteOffset = lowNote;

// define Note as a new type
typedef struct
{
    bool fPattern[10];
    int targetFreq;
    int blowVel;
} Note;

/* fPattern: Array of bools for finger pattern - 1 means hole covered.
 * targetFreq: Pitch of note. Determined from https://www.inspiredacoustics.com/en/MIDI_note_numbers_and_center_frequencies.
 * blowVel: RPM to produce correct pitch note. Currently determined
 *          experimentally. In future to be determined by program.
 */
// create array of Note structures
Note notes[arrSize] = {
    {{1, 1, 1, 1, 1, 1, 1, 1, 1, 1}, 523, 130},  // C5 (MIDI 72)
    {{1, 1, 1, 1, 1, 1, 1, 1, 1, 0}, 554, 140},  // Db5 (MIDI 73)
    {{1, 1, 1, 1, 1, 1, 1, 1, 0, 0}, 587, 150},  // D5 (MIDI 74)
    {{1, 1, 1, 1, 1, 1, 1, 0, 0, 0}, 622, 160},  // Eb5 (MIDI 75)
    {{1, 1, 1, 1, 1, 1, 0, 0, 0, 0}, 659, 170},  // E5 (MIDI 76)
    {{1, 1, 1, 1, 1, 0, 1, 1, 1, 1}, 698, 180},  // F5 (MIDI 77)
    {{1, 1, 1, 1, 0, 1, 1, 1, 0, 0}, 740, 190},  // Gb5 (MIDI 78)
    {{1, 1, 1, 1, 0, 0, 0, 0, 0, 0}, 784, 200},  // G5 (MIDI 79)
    {{1, 1, 1, 0, 1, 1, 1, 0, 0, 0}, 831, 220},  // Ab5 (MIDI 80)
    {{1, 1, 1, 0, 0, 0, 0, 0, 0, 0}, 880, 240},  // A5 (MIDI 81)
    {{1, 1, 0, 1, 1, 0, 0, 0, 0, 0}, 932, 265},  // Bb5 (MIDI 82)
    {{1, 1, 0, 0, 0, 0, 0, 0, 0, 0}, 988, 290},  // B5 (MIDI 83)
    {{1, 0, 1, 0, 0, 0, 0, 0, 0, 0}, 1047, 320}, // C6 (MIDI 84)
    {{0, 1, 1, 0, 0, 0, 0, 0, 0, 0}, 1109, 330}, // Db6 (MIDI 85)
    {{0, 0, 1, 0, 0, 0, 0, 0, 0, 0}, 1175, 340}, // D6 (MIDI 86)
};

// pattern for all fingers released
bool fingersOff[10] = {0, 0, 0, 0, 0, 0, 0, 0, 0, 0};

// define pins the solenoids are connected to in hole order starting with thumb
const int solenoidPins[10] = {45, 47, 49, 51, 53, 37, 35, 39, 41, 43};

// define MIDI channel
// MIDI channels 1-16 are zero based so minus 1 for byte value
const byte channel = 0;

// construct status bytes
// left hex digit represents the command and right digit the channel
const byte noteOn = 0x90 + channel;
const byte noteOff = 0x80 + channel;

/* Don't want to remove fingers immediately after note off command, especially 
 * in the case of repeated notes so leave them energised. However, don't want 
 * them energised forever as that would lead to overheating. A timer is started
 * after a note off command and fingers released if idleWait time reached. 
 */ 
unsigned long idleTimeStart;
const int idleWait = 2000; // ms


/////////////////////////
//    FUNCTION DEFS    //
/////////////////////////

void setFingers(bool pattern[])
{
    for (int f = 0; f < 10; f++)
    {
        // set pin high/low according to pattern
        digitalWrite(solenoidPins[f], pattern[f]);
    }
}

bool isInRange(byte note)
{
    if (note >= lowNote && note <= highNote)
    {
        return true;
    }
    else
    {
        return false;
    }
}

void setRPM(int rpm)
{
    // send rpm to lung module via I2C
    // from Wire Master Writer by Nicholas Zambetti <http://www.zambetti.com>
    Wire.beginTransmission(4); // transmit to device #4
    Wire.write(highByte(rpm)); // sends one byte
    Wire.write(lowByte(rpm));
    Wire.endTransmission(); // stop transmitting
}

void doNoteOn(byte note, byte vel)
{
    // convert from MIDI note number to index in our note array
    int ndx = note - noteOffset;

    #ifdef DEBUG
    Serial.print("Doing NoteOn | ");
    Serial.print("MIDI: ");
    Serial.print(note);
    Serial.print(" | Index: ");
    Serial.println(ndx);
    #endif

    // set fingers
    setFingers(notes[ndx].fPattern);

    // set RPM corresponding to note
    setRPM(notes[ndx].blowVel);
}

void doNoteOff(byte vel)
{
    // stop blowing
    setRPM(0);

    #ifdef DEBUG
    Serial.println("Doing NoteOff");
    #endif

    // record start time of timer
    idleTimeStart = millis();
}


/////////////////////////
//        SETUP        //
/////////////////////////

void setup()
{
    // serial used to receive MIDI and report debugging
    Serial.begin(115200);

    // set all solenoid pins for OUTPUT
    for (int f = 0; f < 10; f++)
    {
        pinMode(solenoidPins[f], OUTPUT);
        digitalWrite(solenoidPins[f], HIGH);
        delay(100);
        digitalWrite(solenoidPins[f], LOW);
    }

    // join i2c bus
    Wire.begin();
}


/////////////////////////
//      MAIN LOOP      //
/////////////////////////
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

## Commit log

2021-10-26 Create High-Precision Regulation of a Pressure Controlled Artificial Mouth.pdf
2021-11-10 First valve prototype design
    STL files for an experimental valve
    [valve-half-ds.stl, valve-half-fan.stl, valve-paddle.stl]
2021-11-10 Mouthpiece parts added
    [mouthpiece-connector.stl, valve-coupler.stl]
2021-11-11 Hardware Concepts - Model A & B
    Hardware concepts for Models A & B - Implementation of Solenoid Actuator
2021-11-19 Create big-blower-nozzle.stl
    Late commit. Red part used for ducting big blower to recorder.
    [big-blower-nozzle.stl]
2021-11-19 New STL files
    Parts that I'm printing for testing the ball valve in line and mocking up a bellow system.
    [bellow-base.stl, bellow-top.stl, big-blower-to-bvalve.stl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]
2021-11-19 Including data analysis of Freq/Voltage
2021-11-19 Create Model C - Built on Design for Hardware - Button Actuation.pdf
    Build of initial actuator concept
2021-11-21 Create solenoid_syncPulse.ino
    Create test code for solenoids
2021-11-30 Create finger_blow_test.ino
    File to test bringing together the different sub systems
2021-11-30 Create solenoid_multiPulse.ino
    Garry's testing
2021-12-03 Create note_test.ino
    added functions to play a specified note by making solenoids high or low
2021-12-03 Create arduino_note_test.ino
    A simple function to actuate the solenoids for a specified note
2021-12-06 Updated folder structure
    [bellow-base.stl, bellow-top.stl, big-blower-nozzle.stl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]
2021-12-08 Testing math with bytes on arduino
2021-12-08 MIDI to arduino working
2021-12-20 Update arduino_main
    Main loop should deal with note on and note off messages and functions written to deal with these commands and actuate fingering. Not tested. Yet to implement blowing
2021-12-21 Update RPi README to explain testing utility. Also update of jukebox_testing.py so won't do anything when not imported
    [jukebox_testing.py]
2021-12-21 Add github link for stepper library
2021-12-29 Draft readme instructions
    Draft instructions created to print and build the recorder fingering module.
2021-12-29 Added lots of prints for debugging
2021-12-29 Update jukebox_testing.py
    add .decode() function to enable printing of hex to string
2021-12-29 Update arduino_main.ino
    Remove non needed print test
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2021-12-30 Revert "Clean up folders and rename"
    This reverts commit b34c5bec976bb41e53cfbf54981e48dd4d0a4ea4.
    [arduino_main.ino, jukebox_testing.py, midi_compatability_test.py]
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2022-01-04 Create 5 Seater Container Body.stl
    [5 Seater Container Body.stl]
2022-01-05 Fixed blower travel direction & operation
    [arduino_main.ino, jukebox_testing.py]
2022-01-06 Create 1 Seater Container Body.stl
    [1 Seater Container Body.stl]
2022-01-06 recorder base frame stl
    [five_seater_container_body.stl, one_seater_contaioner_body.stl, recorder_base_frame_stand.stl]
2022-01-06 folder name change
    [one_seater_container_body.stl]
2022-01-08 Update recorder base frame
    [recorder_base_frame_stand.stl, recorder_base_frame_stand_bottom.stl, recorder_base_frame_stand_top_slider.stl]
2022-01-08 Updated containers and new finger pads
    [finger_pads_middle_joint.stl, five_seater_container_body.stl, one_seater_container_body.stl]
2022-01-09 large double hole finger pad
    [double_hole_finger_pad_large.stl, double_hole_finger_pad_small.stl]
2022-01-09 new readme and fingering module assembly
    [fingering_module_assembly_overview.stl]
2022-01-09 Update folders for obj files
    [recorder_base_frame_stand_top.stl, square_finger_pad.stl]
2022-01-09 added .obj files for easy use across 3D printing platforms
    [double_hole_finger_pad_large.obj, double_hole_finger_pad_small.obj, five_seater_container_body.obj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]
2022-01-09 New recorder clamp models
    [recorder_clamp_bottom.obj, recorder_clamp_bottom.stl, recorder_clamp_top.obj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]
2022-01-10 Rename Folders
    [bellow-base.stl, bellow-top.stl, big-blower-nozzle.stl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]
2022-01-10 Change to blowing, BOM for blower done
    [big-blower-nozzle.stl, big-blower-to-bvalve.stl, bvalve-to-mouthpiece.stl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]
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2022-01-11 STEP files added
    [Blowing Module.step, Fingering Module.step, double_hole_finger_pad_large.obj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]
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2022-01-13 Changed finger off behaviour to wait 1 second after note has played
2022-01-13 New two seater body
    [two_seater_body.stl]
2022-01-13 update file name
    [two_seater_container_body.stl]
2022-01-16 solenoid boxes
    [double_tone_hole_single_box.3mf, single_tone_hole_single_box.3mf]
2022-01-17 Test fingertips
    [finger tip 1 v1.3mf, finger tip 1 v2.3mf, finger tip 1 v3.3mf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]
2022-01-17 3mfs of brackets to hold recorder
    [Holder_lower.3mf, Holder_upper.3mf]
2022-01-17 mesh of five seat box
    [single_tone_hole_five_box.3mf]
2022-01-17 more fingertips
    [finger tip double big v2.3mf, finger tip double small v2.3mf]
2022-02-13 Code for blowing system on own board. Control 2 steppers from one board receiving desired blowing vel by I2C.
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2022-02-14 Twin lung system receiving over I2C. Preliminary tests passed.
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2022-07-28 added stand
    [Stand v1.3mf]
2022-08-01 Upload new model files and delete old
    3MF files for fingering module added. All STLs replaced. Redundant models removed.
    [double_hole_finger_pad_large.stl, double_hole_finger_pad_small.stl, double_tone_hole_extension_arm.stl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]
2022-08-01 New assembly file updated
    [Fingering Module.step]
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2022-08-04 Update mouthpiece connector to 3mf
    [pipe-to-mouthpiece.3mf, pipe-to-mouthpiece.stl]
2022-08-04 Update all models to current design in 3mf format
    [bearing-support.3mf, bottom-cap-support.3mf, bottom-cap.3mf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]
2022-08-04 Update STEP assembly
    [Blowing Module.step]
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2022-08-04 Update assembly instructions and corrections
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
